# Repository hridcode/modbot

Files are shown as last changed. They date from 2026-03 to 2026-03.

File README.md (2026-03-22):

# ModBot

ModBot is a versatile RP2040 development board/robot base for mini robots. It is relatively small (~80x50mm), but packs a punch.

# Features

- RP2040 chip
- 2 L293D IC motor drivers (capable of driving 4 motors)
- MPU-6050 gyroscope + accelerometer IC
- 12 digital GPIO expansion pins 
- 4 ADC GPIO expansion pins
- 16 connections each for GND, +3.3V, and +5V (VBUS)
- Battery connection
- USB-C support (bare minimum for 2026)

# Pictures

|Schematic|PCB|
|---|---|
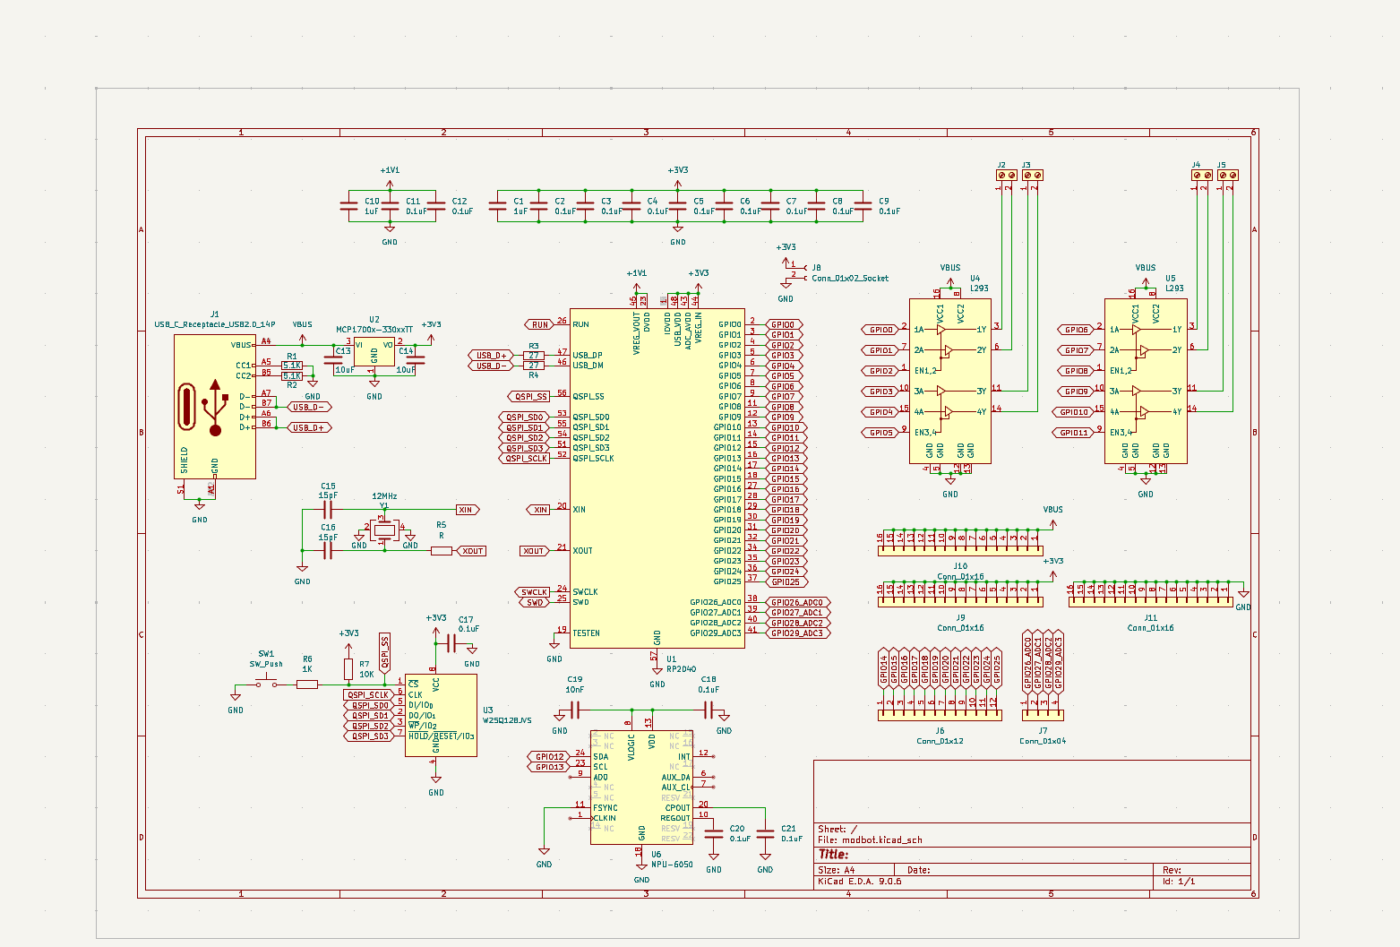
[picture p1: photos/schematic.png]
Image of schematic
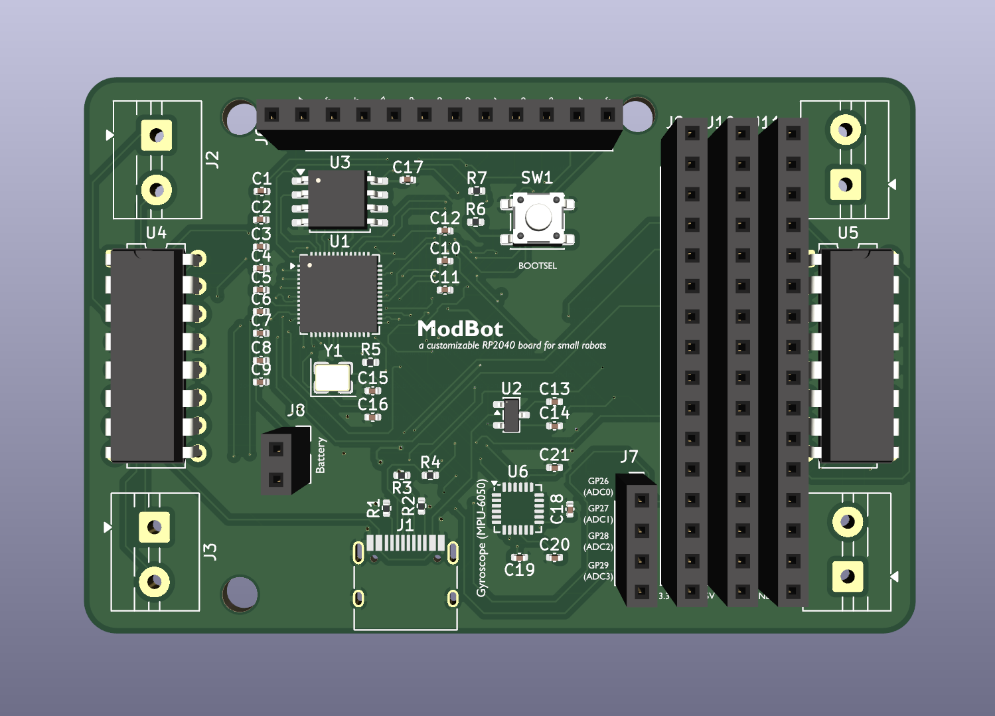
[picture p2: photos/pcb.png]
Image of PCB
|||

# Notes

- If you are to use a battery with the board, you must include your own charging board and switch.
- I don't do FRC/FTC so I don't know if this would be something you can use for that.

---

Have fun!

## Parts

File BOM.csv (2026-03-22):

Item | Count | Price | Source
RP2040 chip | 1 | 0.80 | https://www.digikey.com/en/products/detail/raspberry-pi/SC0914-7/14306013
MPU-6050 chip | 1 | 2.61 | https://robu.in/product/mpu-6050-qfn-24-3-axis-gyro-accelerometer-ic/
USB-C receptacle | 1 | 0.16 | https://www.aliexpress.us/item/3256809252183783.html?curPageLogUid=jFPWhVMXh8P0
W25Q128JVSIQ flash memory chip | 1 | 2.24 | https://www.digikey.com/en/products/detail/winbond-electronics/W25Q128JVSIQ/5803943
12MHz crystal | 1 | 0.59 | https://www.digikey.com/en/products/detail/w%C3%BCrth-elektronik/830069944/13979393
6x6mm SMD button | 1 | 0.10 | https://www.aliexpress.us/item/3256807370530791.html?curPageLogUid=4020PjtAwq6e
Screw terminal (2 pin | 2.54mm pitch) | 4 | 0.88 | https://www.aliexpress.us/item/3256802993168222.html?curPageLogUid=YEyRhjFtVRE9
L293D motor driver chip | 2 | 0.58 | https://www.aliexpress.us/item/3256807177813062.html?curPageLogUid=ljwkACuWUc54
PCB | 1 | 0.4 | https://cart.jlcpcb.com/quote?stencilLayer=2&stencilWidth=80&stencilLength=50&stencilCounts=5&plateType=1
Total |  | 8.36

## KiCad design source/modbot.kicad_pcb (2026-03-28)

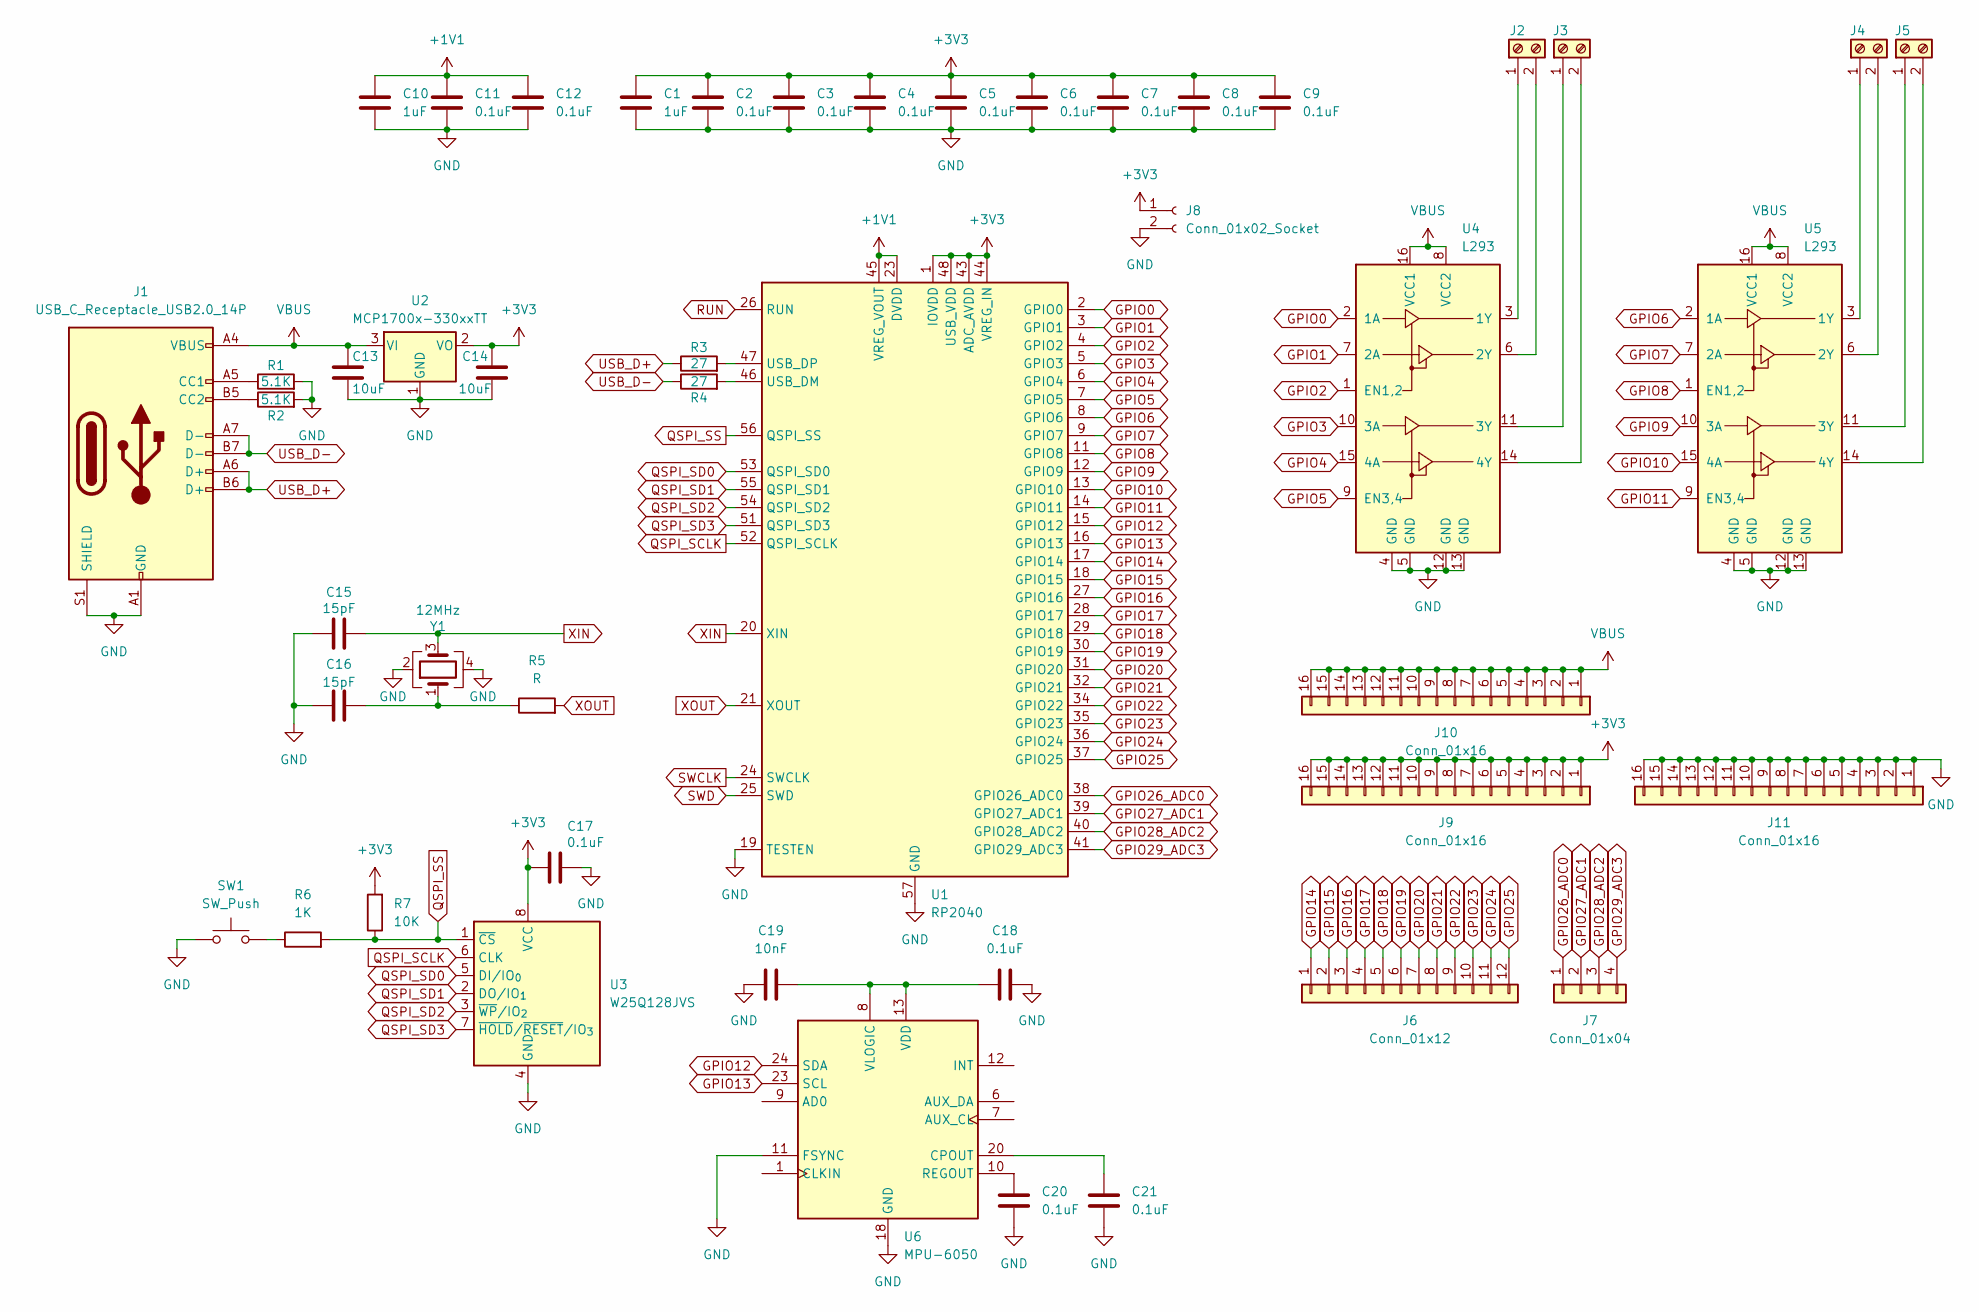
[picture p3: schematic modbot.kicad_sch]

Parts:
C1, C10: 1uF; C_0402_1005Metric
C2, C3, C4, C5, C6, C7, C8, C9, C11, C12, C17, C18, C20, C21: 0.1uF; C_0402_1005Metric
C13, C14: 10uF; C_0402_1005Metric
C15, C16: 15pF; C_0402_1005Metric
C19: 10nF; C_0402_1005Metric
J1: USB_C_Receptacle_USB2.0_14P; USB_C_Receptacle_HRO_TYPE-C-31-M-12
J2, J3, J4, J5: Screw_Terminal_01x02; TerminalBlock_MaiXu_MX126-5.0-02P_1x02_P5.00mm
J6: Conn_01x12; PinSocket_1x12_P2.54mm_Vertical
J7: Conn_01x04; PinSocket_1x04_P2.54mm_Vertical
J8: Conn_01x02_Socket; PinSocket_1x02_P2.54mm_Vertical
J9, J10, J11: Conn_01x16; PinSocket_1x16_P2.54mm_Vertical
R1, R2: 5.1K; R_0402_1005Metric
R3, R4: 27; R_0402_1005Metric
R5: R; R_0402_1005Metric
R6: 1K; R_0402_1005Metric
R7: 10K; R_0402_1005Metric
SW1: SW_Push; SW_SPST_PTS647_Sx38
U1: RP2040; QFN-56-1EP_7x7mm_P0.4mm_EP3.2x3.2mm
U2: MCP1700x-330xxTT; SOT-23
U3: W25Q128JVS; SOIC-8_5.3x5.3mm_P1.27mm
U4, U5: L293; DIP-16_W7.62mm
U6: MPU-6050; InvenSense_QFN-24_4x4mm_P0.5mm
Y1: 12MHz; Crystal_SMD_3225-4Pin_3.2x2.5mm

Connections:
+1V1: C10.1, C11.1, C12.1, U1.23 (DVDD), U1.45 (VREG_VOUT), U1.50 (DVDD)
+3V3: C1.1, C2.1, C3.1, C4.1, C5.1, C6.1, C7.1, C8.1, C9.1, C14.1, C17.1, J8.1, J9.1, J9.2, J9.3, J9.4, J9.5, J9.6, J9.7, J9.8, J9.9, J9.10, J9.11, J9.12, J9.13, J9.14, J9.15, J9.16, R7.2, U1.1 (IOVDD), U1.10 (IOVDD), U1.22 (IOVDD), U1.33 (IOVDD), U1.42 (IOVDD), U1.43 (ADC_AVDD), U1.44 (VREG_IN), U1.48 (USB_VDD), U1.49 (IOVDD), U2.2 (VO), U3.8 (VCC)
GND: C1.2, C2.2, C3.2, C4.2, C5.2, C6.2, C7.2, C8.2, C9.2, C10.2, C11.2, C12.2, C13.2, C14.2, C15.1, C16.1, C17.2, C18.2, C19.1, C20.1, C21.1, J1.A1 (GND), J1.A12 (GND), J1.B1 (GND), J1.B12 (GND), J1.S1 (SHIELD), J8.2, J11.1, J11.2, J11.3, J11.4, J11.5, J11.6, J11.7, J11.8, J11.9, J11.10, J11.11, J11.12, J11.13, J11.14, J11.15, J11.16, R1.2, R2.2, SW1.1, U1.19 (TESTEN), U1.57 (GND), U2.1 (GND), U3.4 (GND), U4.4 (GND), U4.5 (GND), U4.12 (GND), U4.13 (GND), U5.4 (GND), U5.5 (GND), U5.12 (GND), U5.13 (GND), U6.11 (FSYNC), U6.18 (GND), Y1.2, Y1.4
GPIO0: U1.2 (GPIO0), U4.2 (1A)
GPIO1: U1.3 (GPIO1), U4.7 (2A)
GPIO2: U1.4 (GPIO2), U4.1 (EN1,2)
GPIO3: U1.5 (GPIO3), U4.10 (3A)
GPIO4: U1.6 (GPIO4), U4.15 (4A)
GPIO5: U1.7 (GPIO5), U4.9 (EN3,4)
GPIO6: U1.8 (GPIO6), U5.2 (1A)
GPIO7: U1.9 (GPIO7), U5.7 (2A)
GPIO8: U1.11 (GPIO8), U5.1 (EN1,2)
GPIO9: U1.12 (GPIO9), U5.10 (3A)
GPIO10: U1.13 (GPIO10), U5.15 (4A)
GPIO11: U1.14 (GPIO11), U5.9 (EN3,4)
GPIO12: U1.15 (GPIO12), U6.24 (SDA)
GPIO13: U1.16 (GPIO13), U6.23 (SCL)
GPIO14: J6.1, U1.17 (GPIO14)
GPIO15: J6.2, U1.18 (GPIO15)
GPIO16: J6.3, U1.27 (GPIO16)
GPIO17: J6.4, U1.28 (GPIO17)
GPIO18: J6.5, U1.29 (GPIO18)
GPIO19: J6.6, U1.30 (GPIO19)
GPIO20: J6.7, U1.31 (GPIO20)
GPIO21: J6.8, U1.32 (GPIO21)
GPIO22: J6.9, U1.34 (GPIO22)
GPIO23: J6.10, U1.35 (GPIO23)
GPIO24: J6.11, U1.36 (GPIO24)
GPIO25: J6.12, U1.37 (GPIO25)
GPIO26_ADC0: J7.1, U1.38 (GPIO26_ADC0)
GPIO27_ADC1: J7.2, U1.39 (GPIO27_ADC1)
GPIO28_ADC2: J7.3, U1.40 (GPIO28_ADC2)
GPIO29_ADC3: J7.4, U1.41 (GPIO29_ADC3)
unnamed: C16.2, R5.1, Y1.1
unnamed: J1.A5 (CC1), R1.1
unnamed: J1.B5 (CC2), R2.1
unnamed: J2.1, U4.3 (1Y)
unnamed: J2.2, U4.6 (2Y)
unnamed: J3.1, U4.11 (3Y)
unnamed: J3.2, U4.14 (4Y)
unnamed: J4.1, U5.3 (1Y)
unnamed: J4.2, U5.6 (2Y)
unnamed: J5.1, U5.11 (3Y)
unnamed: J5.2, U5.14 (4Y)
unnamed: R6.1, SW1.2
unnamed: R4.2, U1.46 (USB_DM)
unnamed: R3.2, U1.47 (USB_DP)
unnamed: C21.2, U6.20 (CPOUT)
unnamed: C20.2, U6.10 (REGOUT)
unnamed: C18.1, C19.2, U6.8 (VLOGIC), U6.13 (VDD)
QSPI_SCLK: U1.52 (QSPI_SCLK), U3.6 (CLK)
QSPI_SD0: U1.53 (QSPI_SD0), U3.5 (DI/IO_{0})
QSPI_SD1: U1.55 (QSPI_SD1), U3.2 (DO/IO_{1})
QSPI_SD2: U1.54 (QSPI_SD2), U3.3 (~WP/IO_{2})
QSPI_SD3: U1.51 (QSPI_SD3), U3.7 (~HOLD/~RESET/IO_{3})
QSPI_SS: R6.2, R7.1, U1.56 (QSPI_SS), U3.1 (~CS)
RUN: U1.26 (RUN)
SWCLK: U1.24 (SWCLK)
SWD: U1.25 (SWD)
USB_D+: J1.A6 (D+), J1.B6 (D+), R3.1
USB_D-: J1.A7 (D-), J1.B7 (D-), R4.1
VBUS: C13.1, J1.A4 (VBUS), J1.A9 (VBUS), J1.B4 (VBUS), J1.B9 (VBUS), J10.1, J10.2, J10.3, J10.4, J10.5, J10.6, J10.7, J10.8, J10.9, J10.10, J10.11, J10.12, J10.13, J10.14, J10.15, J10.16, U2.3 (VI), U4.8 (VCC2), U4.16 (VCC1), U5.8 (VCC2), U5.16 (VCC1)
XIN: C15.2, U1.20 (XIN), Y1.3
XOUT: R5.2, U1.21 (XOUT)

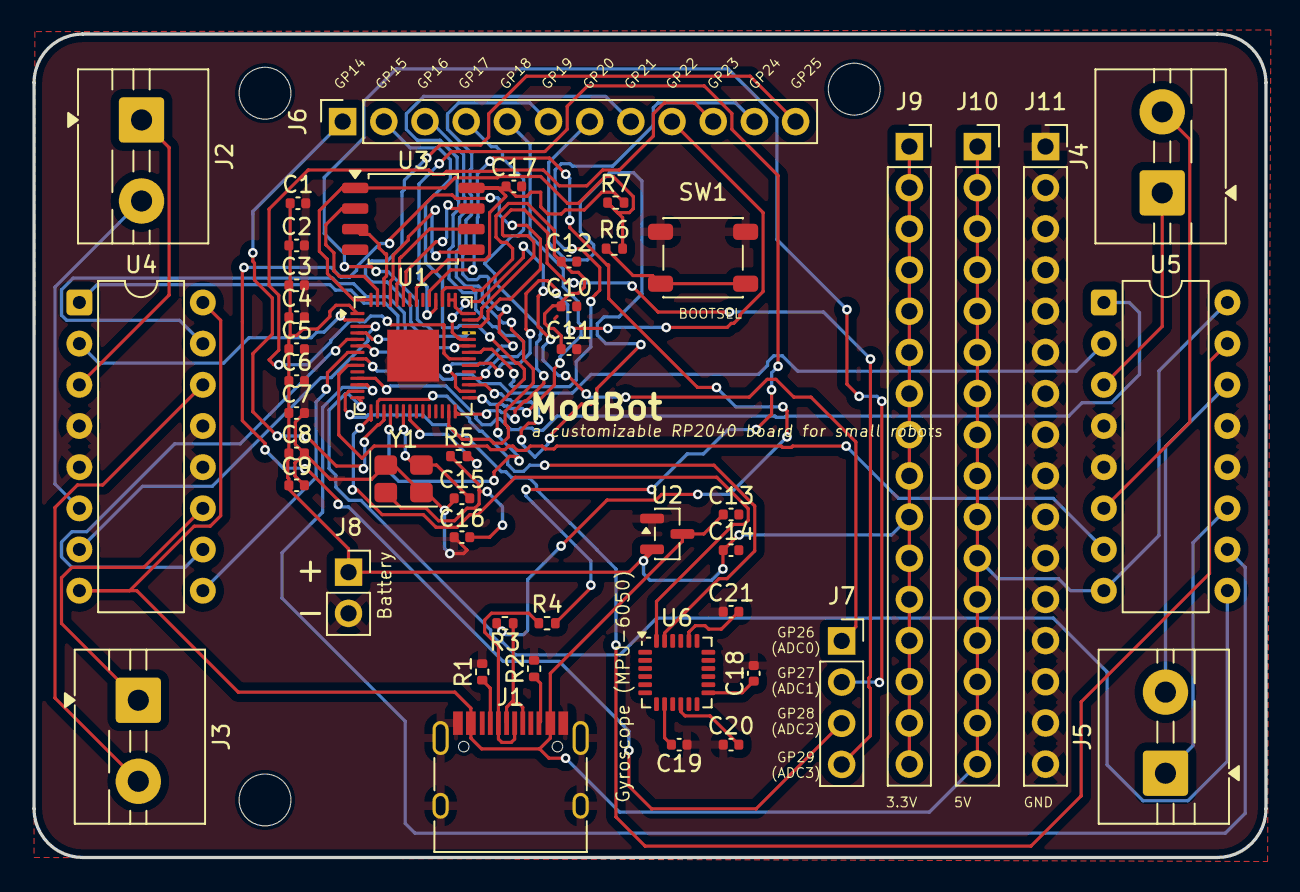
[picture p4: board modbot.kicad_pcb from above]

Board: 2 copper layers, 76.0 x 50.8 mm, 47 parts (0 on the bottom side), 61 nets.

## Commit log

2026-03-22 Added source, production, BOM and README
    [modbot.kicad_pcb, modbot.kicad_sch]
2026-03-22 Updated README.md and BOM.csv
    [BOM.csv]
2026-03-22 Updated BOM.csv
    [BOM.csv]
2026-03-28 Replaced PCB gerber & source files with new versions
    [modbot.kicad_pcb]
